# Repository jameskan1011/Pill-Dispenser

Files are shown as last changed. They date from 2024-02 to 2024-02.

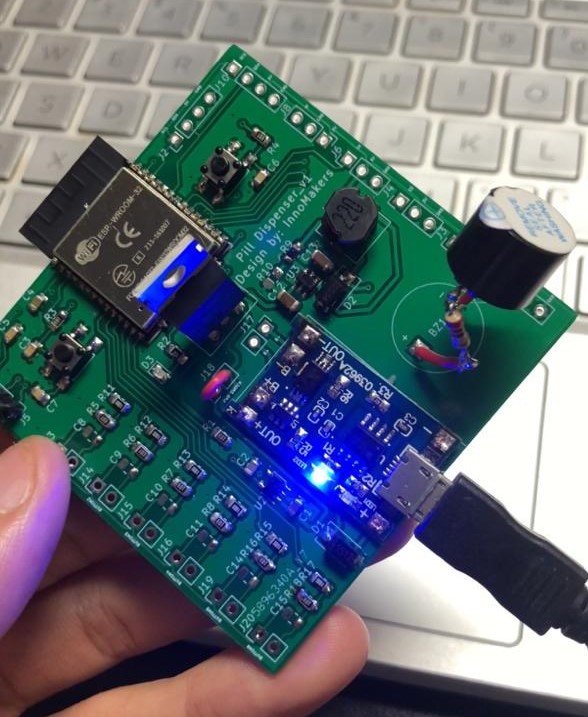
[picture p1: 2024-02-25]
Pictures/pcb.jpeg

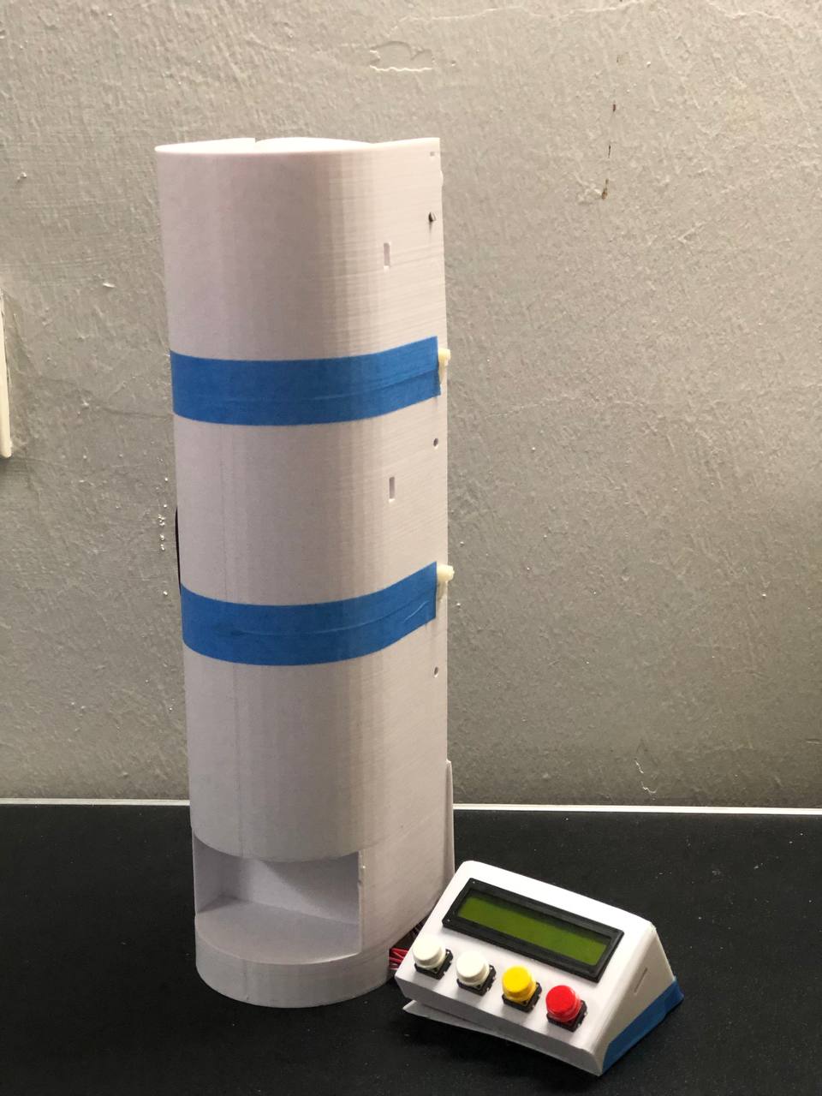
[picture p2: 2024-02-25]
Pictures/dispenser1.jpeg

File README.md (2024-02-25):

# Pill-Dispenser
Pill Dispensir with onboard settings that let you customize reminders for your meds.
<br />• Can be stack for multiple types of pill
<br />• Buzzer alert
<br />• Pill drop count
<br />• Customize time and quantities for meds.

dispenser1
pcb

https://github.com/jameskan1011/Pill-Dispenser/assets/66528008/c5491cce-084c-414e-90f5-08d18c687c19

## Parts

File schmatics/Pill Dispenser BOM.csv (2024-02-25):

Source: | C:\Users\KAN CHANG FEI\Documents\KiCad\6.0\projects\Pill Dispenser\Pill Dispenser\Pill Dispenser.kicad_sch
Date: | 4/19/2023 23:44
Tool: | Eeschema (6.0.5)
Generator: | C:\Program Files\KiCad\6.0\bin\scripting\plugins/bom_csv_grouped_by_value.py
Component Count: | 61
Collated Components:
Item | Qty | Reference(s) | Value | Unit Price | Cost | LibPart | Footprint | Datasheet
1 | 1 | BZ1 | Buzzer |  |  | Device:Buzzer | Buzzer_Beeper:Buzzer_12x9.5RM7.6 | ~
2 | 1 | C1 | 4.7uF |  |  | Device:C | Capacitor_SMD:C_0805_2012Metric | ~
3 | 2 | C2, C4 | 10uF |  |  | Device:C | Capacitor_SMD:C_0805_2012Metric | ~
4 | 10 | C3, C5, C6, C7, C8, C9, C10, C11, C14, C15 | 0.1uF |  |  | Device:C | Capacitor_SMD:C_0805_2012Metric | ~
5 | 2 | C12, C13 | 47uF |  |  | Device:C | Capacitor_SMD:C_0805_2012Metric | ~
6 | 1 | D1 | SS12 |  |  | Device:D_Schottky | Diode_SMD:D_SMA | ~
7 | 1 | D2 | SS34 |  |  | Device:D_Schottky | Diode_SMD:D_SMA | ~
8 | 1 | D3 | LED |  |  | Device:LED | LED_SMD:LED_0805_2012Metric | ~
9 | 1 | J1 | Servo1 |  |  | Connector:Conn_01x03_Male | Connector_PinHeader_2.54mm:PinHeader_1x03_P2.54mm_Vertical | ~
10 | 1 | J2 | LCD Display |  |  | Connector:Conn_01x04_Male | Connector_PinHeader_2.54mm:PinHeader_1x04_P2.54mm_Vertical | ~
11 | 1 | J3 | Servo2 |  |  | Connector:Conn_01x03_Male | Connector_PinHeader_2.54mm:PinHeader_1x03_P2.54mm_Vertical | ~
12 | 1 | J4 | Servo3 |  |  | Connector:Conn_01x03_Male | Connector_PinHeader_2.54mm:PinHeader_1x03_P2.54mm_Vertical | ~
13 | 1 | J5 | UART |  |  | Connector:Conn_01x04_Male | Connector_PinHeader_2.54mm:PinHeader_1x04_P2.54mm_Vertical | ~
14 | 1 | J6 | Servo4 |  |  | Connector:Conn_01x03_Male | Connector_PinHeader_2.54mm:PinHeader_1x03_P2.54mm_Vertical | ~
15 | 1 | J8 | IR |  |  | Connector:Conn_01x03_Male | Connector_PinHeader_2.54mm:PinHeader_1x03_P2.54mm_Vertical | ~
16 | 1 | J10 | RTC | 12.5 | 12.5 | Connector:Conn_01x04_Male | Connector_PinHeader_2.54mm:PinHeader_1x04_P2.54mm_Vertical | ~
17 | 1 | J13 | Button1 |  |  | Connector:Conn_01x02_Male | Connector_PinHeader_2.54mm:PinHeader_1x02_P2.54mm_Vertical | ~
18 | 1 | J14 | Button2 |  |  | Connector:Conn_01x02_Male | Connector_PinHeader_2.54mm:PinHeader_1x02_P2.54mm_Vertical | ~
19 | 1 | J15 | Button3 |  |  | Connector:Conn_01x02_Male | Connector_PinHeader_2.54mm:PinHeader_1x02_P2.54mm_Vertical | ~
20 | 1 | J16 | Button4 |  |  | Connector:Conn_01x02_Male | Connector_PinHeader_2.54mm:PinHeader_1x02_P2.54mm_Vertical | ~
21 | 1 | J17 | BAttery |  |  | Connector:Conn_01x02_Male | Connector_PinHeader_2.54mm:PinHeader_1x02_P2.54mm_Vertical | ~
22 | 1 | J18 | Power Switch |  |  | Connector:Conn_01x02_Male | Connector_PinHeader_2.54mm:PinHeader_1x02_P2.54mm_Vertical | ~
23 | 1 | J19 | Button5 |  |  | Connector:Conn_01x02_Male | Connector_PinHeader_2.54mm:PinHeader_1x02_P2.54mm_Vertical | ~
24 | 1 | J20 | Button6 |  |  | Connector:Conn_01x02_Male | Connector_PinHeader_2.54mm:PinHeader_1x02_P2.54mm_Vertical | ~
25 | 1 | L1 | 22uH |  |  | pspice:INDUCTOR | Inductor_SMD:L_7.3x7.3_H4.5 | ~
26 | 1 | Q1 | IRF4905 |  |  | Transistor_FET:IRF9540N | Package_TO_SOT_THT:TO-220-3_Vertical | http://www.irf.com/product-info/datasheets/data/irf9540n.pdf
27 | 9 | R1, R3, R4, R5, R6, R7, R8, R16, R18 | 10K |  |  | Device:R | Resistor_SMD:R_0805_2012Metric_Pad1.20x1.40mm_HandSolder | ~
28 | 1 | R2 | 1K |  |  | Device:R | Resistor_SMD:R_0805_2012Metric_Pad1.20x1.40mm_HandSolder | ~
29 | 1 | R9 | 14.7K |  |  | Device:R | Resistor_SMD:R_0805_2012Metric_Pad1.20x1.40mm_HandSolder | ~
30 | 1 | R10 | 2K |  |  | Device:R | Resistor_SMD:R_0805_2012Metric_Pad1.20x1.40mm_HandSolder | ~
31 | 6 | R11, R12, R13, R14, R15, R17 | 100 |  |  | Device:R | Resistor_SMD:R_0805_2012Metric_Pad1.20x1.40mm_HandSolder | ~
32 | 2 | SW1, SW2 | SW_SPST |  |  | Switch:SW_SPST | Button_Switch_SMD:SW_SPST_TL3305A | ~
33 | 1 | U1 | TP4056_Module |  |  | My_Design:TP4056_Module | My_Design:TP4056_Module
34 | 1 | U2 | AP7366-33W5-7 |  |  | Regulator_Linear:MIC5504-3.3YM5 | Package_TO_SOT_SMD:SOT-23-5_HandSoldering | http://ww1.microchip.com/downloads/en/DeviceDoc/MIC550X.pdf
35 | 1 | U3 | MT3608 |  |  | Regulator_Switching:MT3608 | Package_TO_SOT_SMD:SOT-23-6 | https://www.olimex.com/Products/Breadboarding/BB-PWR-3608/resources/MT3608.pdf
36 | 1 | U4 | ESP32-WROOM-32 | 10 | 10 | RF_Module:ESP32-WROOM-32 | RF_Module:ESP32-WROOM-32 | https://www.espressif.com/sites/default/files/documentation/esp32-wroom-32_datasheet_en.pdf

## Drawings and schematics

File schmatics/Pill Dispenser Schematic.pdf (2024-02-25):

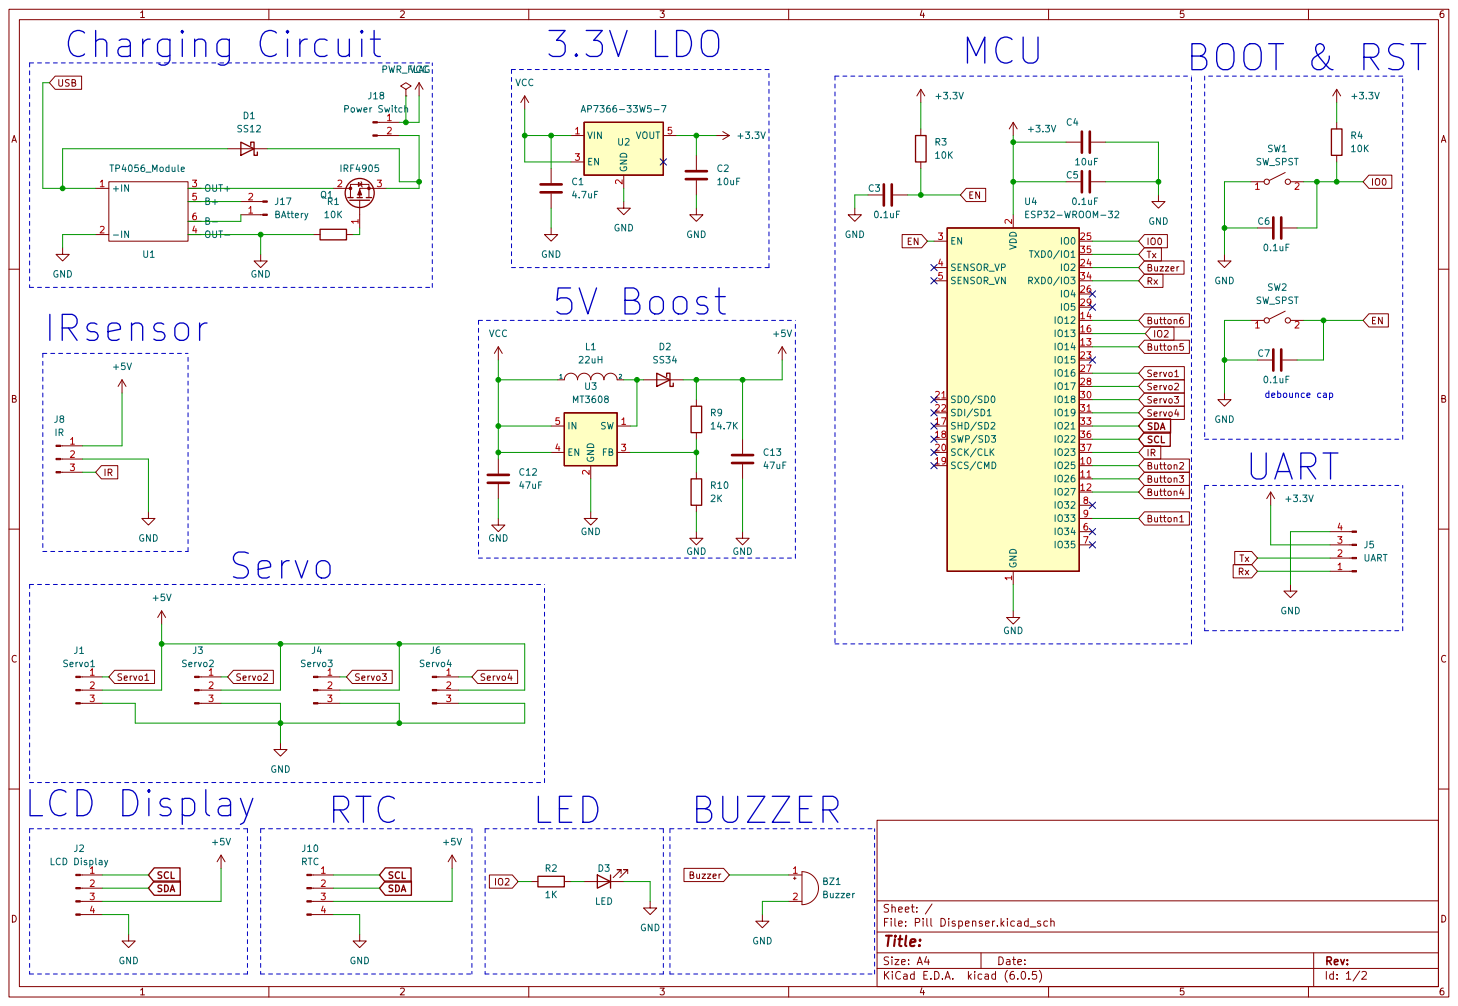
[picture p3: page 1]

2 EN 3 VOUT 5 U2 AP7366-33W5-7 D2 SS34 GND GNDGND

2 SCK/CLK 20 SDO/SD0 21 SDI/SD1 22

File: Pill Dispenser.kicad_sch Sheet: / Untitled Sheet File: untitled.kicad_sch

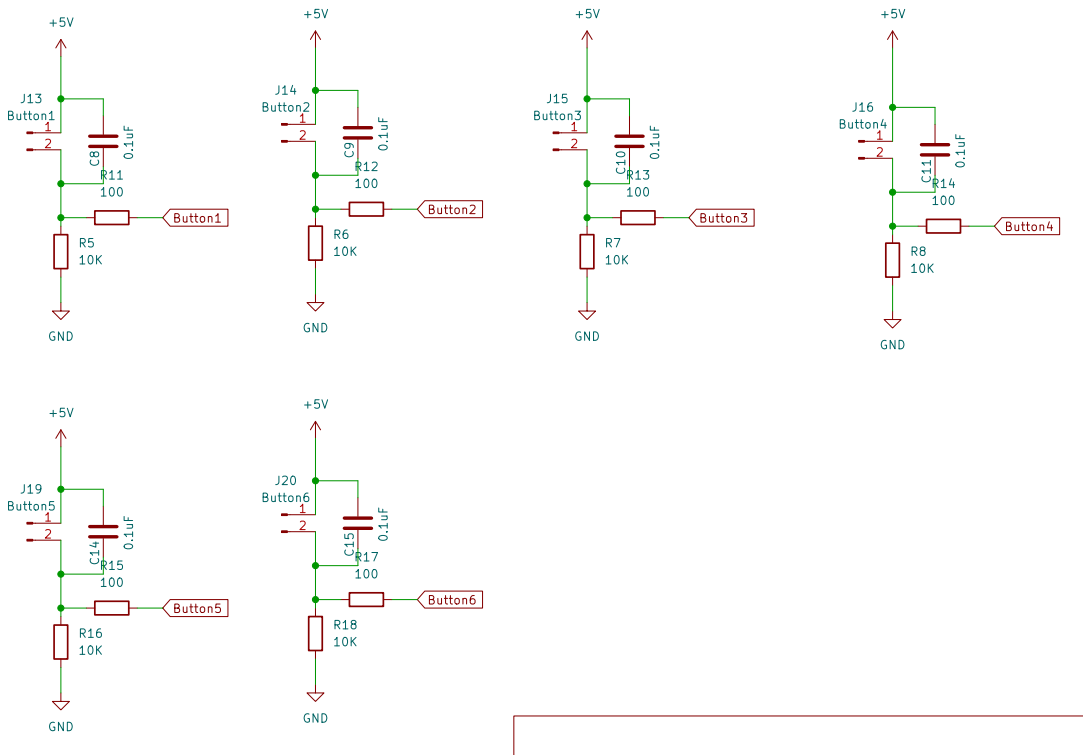
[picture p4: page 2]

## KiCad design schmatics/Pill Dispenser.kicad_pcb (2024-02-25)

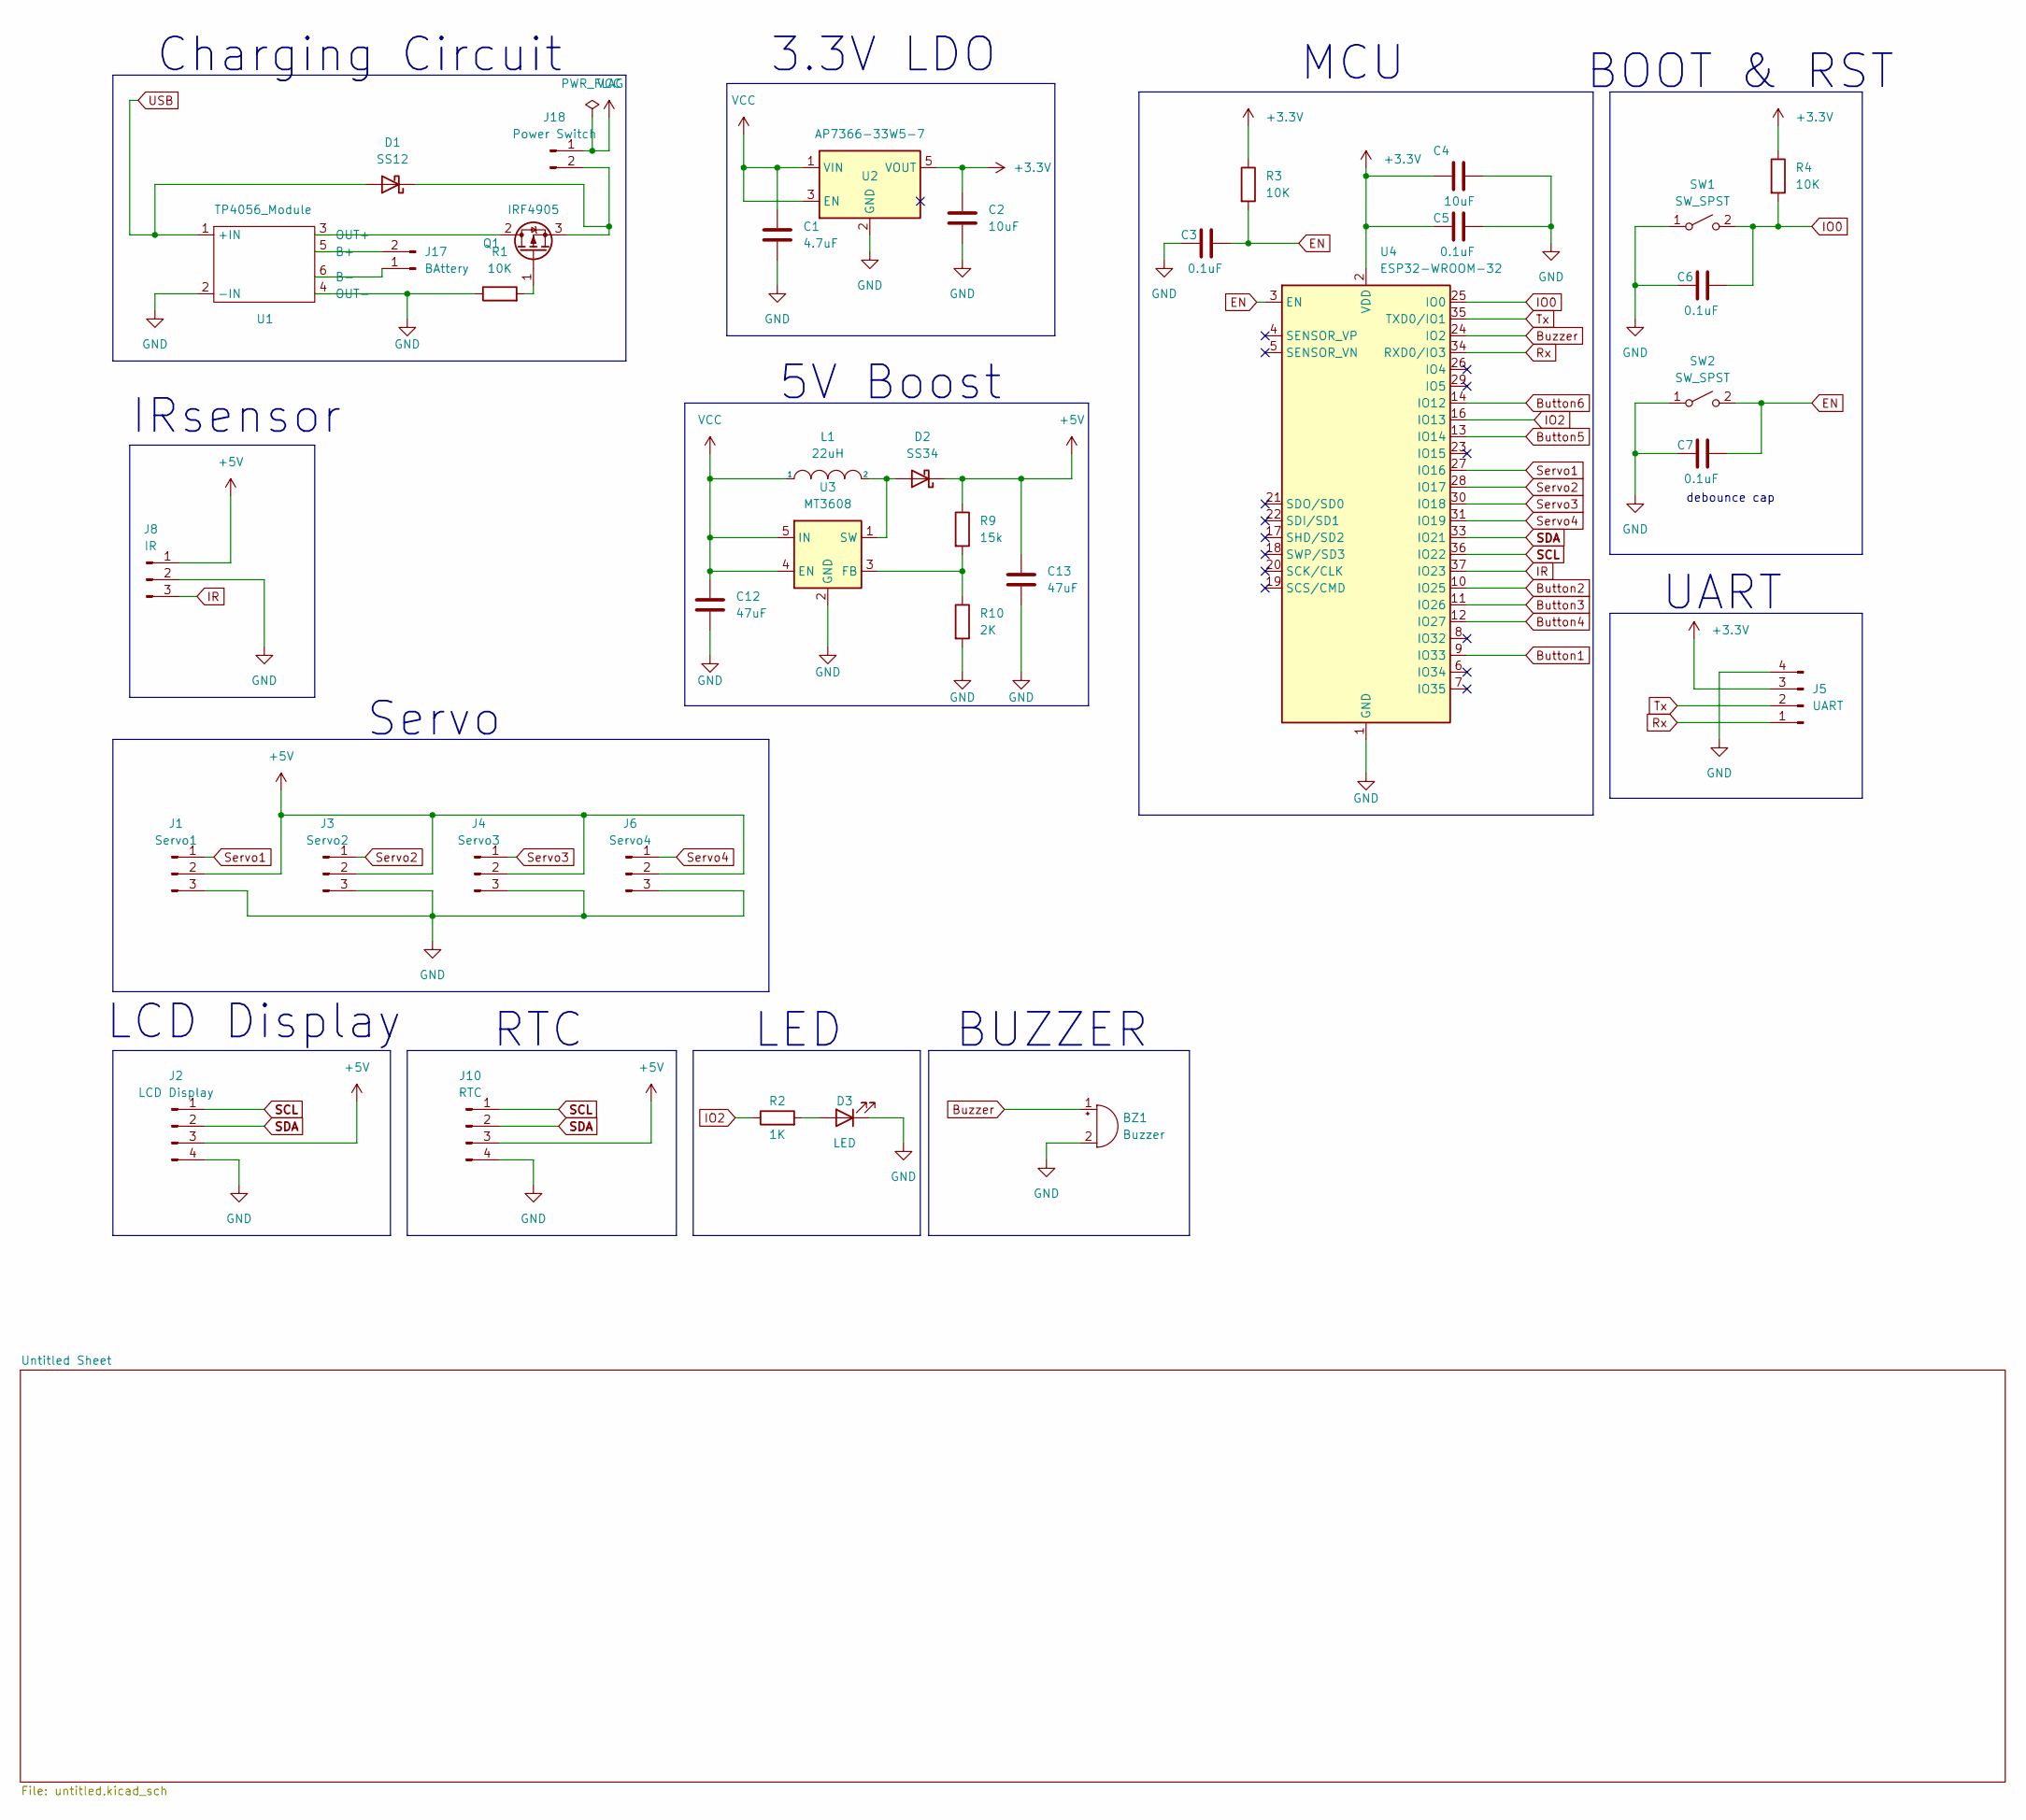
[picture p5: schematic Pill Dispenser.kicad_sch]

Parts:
BZ1: Buzzer; Buzzer_12x9.5RM7.6
C1: 4.7uF; C_0805_2012Metric
C2, C4: 10uF; C_0805_2012Metric
C3, C5, C6, C7: 0.1uF; C_0805_2012Metric
C12, C13: 47uF; C_0805_2012Metric
D1: SS12; D_SMA
D2: SS34; D_SMA
D3: LED; LED_0805_2012Metric
J1: Servo1; PinHeader_1x03_P2.54mm_Vertical
J2: LCD Display; PinHeader_1x04_P2.54mm_Vertical
J3: Servo2; PinHeader_1x03_P2.54mm_Vertical
J4: Servo3; PinHeader_1x03_P2.54mm_Vertical
J5: UART; PinHeader_1x04_P2.54mm_Vertical
J6: Servo4; PinHeader_1x03_P2.54mm_Vertical
J8: IR; PinHeader_1x03_P2.54mm_Vertical
J10: RTC; PinHeader_1x04_P2.54mm_Vertical
J17: BAttery; PinHeader_1x02_P2.54mm_Vertical
J18: Power Switch; PinHeader_1x02_P2.54mm_Vertical
L1: 22uH; L_7.3x7.3_H4.5
Q1: IRF4905; TO-220-3_Vertical
R1, R3, R4: 10K; R_0805_2012Metric_Pad1.20x1.40mm_HandSolder
R2: 1K; R_0805_2012Metric_Pad1.20x1.40mm_HandSolder
R9: 15k; R_0805_2012Metric_Pad1.20x1.40mm_HandSolder
R10: 2K; R_0805_2012Metric_Pad1.20x1.40mm_HandSolder
SW1, SW2: SW_SPST; SW_SPST_TL3305A
U1: TP4056_Module
U2: AP7366-33W5-7; SOT-23-5_HandSoldering
U3: MT3608; SOT-23-6
U4: ESP32-WROOM-32

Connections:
+3V3: C2.1, C4.1, C5.1, J5.3, R3.1, R4.1, U2.5 (VOUT), U4.2 (VDD)
+5V: C13.1, D2.1 (K), J1.2, J2.3, J3.2, J4.2, J6.2, J8.1, J10.3, R9.1; also elsewhere on the board
Button1: U4.9 (IO33); also elsewhere on the board
Button2: U4.10 (IO25); also elsewhere on the board
Button3: U4.11 (IO26); also elsewhere on the board
Button4: U4.12 (IO27); also elsewhere on the board
Button5: U4.13 (IO14); also elsewhere on the board
Button6: U4.14 (IO12); also elsewhere on the board
Buzzer: BZ1.1 (-), U4.24 (IO2)
EN: C3.2, C7.2, R3.2, SW2.2 (B), U4.3 (EN)
GND: BZ1.2 (+), C1.2, C2.2, C3.1, C4.2, C5.2, C6.1, C7.1, C12.2, C13.2, D3.1 (K), J1.3, J2.4, J3.3, J4.3, J5.4, J6.3, J8.2, J10.4, R1.1, R10.2, SW1.1 (A), SW2.1 (A), U1.2 (-IN), U1.4 (OUT-), U2.2 (GND), U3.2 (GND), U4.1 (GND), U4.15 (GND), U4.38 (GND), U4.39 (GND); also elsewhere on the board
IO0: C6.2, R4.2, SW1.2 (B), U4.25 (IO0)
IO2: R2.1, U4.16 (IO13)
IR: J8.3, U4.37 (IO23)
unnamed: D1.1 (K), J18.2, Q1.3 (S)
unnamed: D2.2 (A), L1.2, U3.1 (SW)
unnamed: D3.2 (A), R2.2
unnamed: J17.1, U1.6 (B-)
unnamed: J17.2, U1.5 (B+)
unnamed: Q1.1 (G), R1.2
unnamed: Q1.2 (D), U1.3 (OUT+)
unnamed: R9.2, R10.1, U3.3 (FB)
Rx: J5.1, U4.34 (RXD0/IO3)
SCL: J2.1, J10.1, U4.36 (IO22)
SDA: J2.2, J10.2, U4.33 (IO21)
Servo1: J1.1, U4.27 (IO16)
Servo2: J3.1, U4.28 (IO17)
Servo3: J4.1, U4.30 (IO18)
Servo4: J6.1, U4.31 (IO19)
Tx: J5.2, U4.35 (TXD0/IO1)
USB: D1.2 (A), U1.1 (+IN)
VCC: C1.1, C12.1, J18.1, L1.1, U2.1 (VIN), U2.3 (EN), U3.4 (EN), U3.5 (IN)

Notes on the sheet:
Charging Circuit
Servo
MCU
BOOT & RST
3.3V LDO
LCD Display
5V Boost
BUZZER
debounce cap
LED
UART
RTC
IRsensor

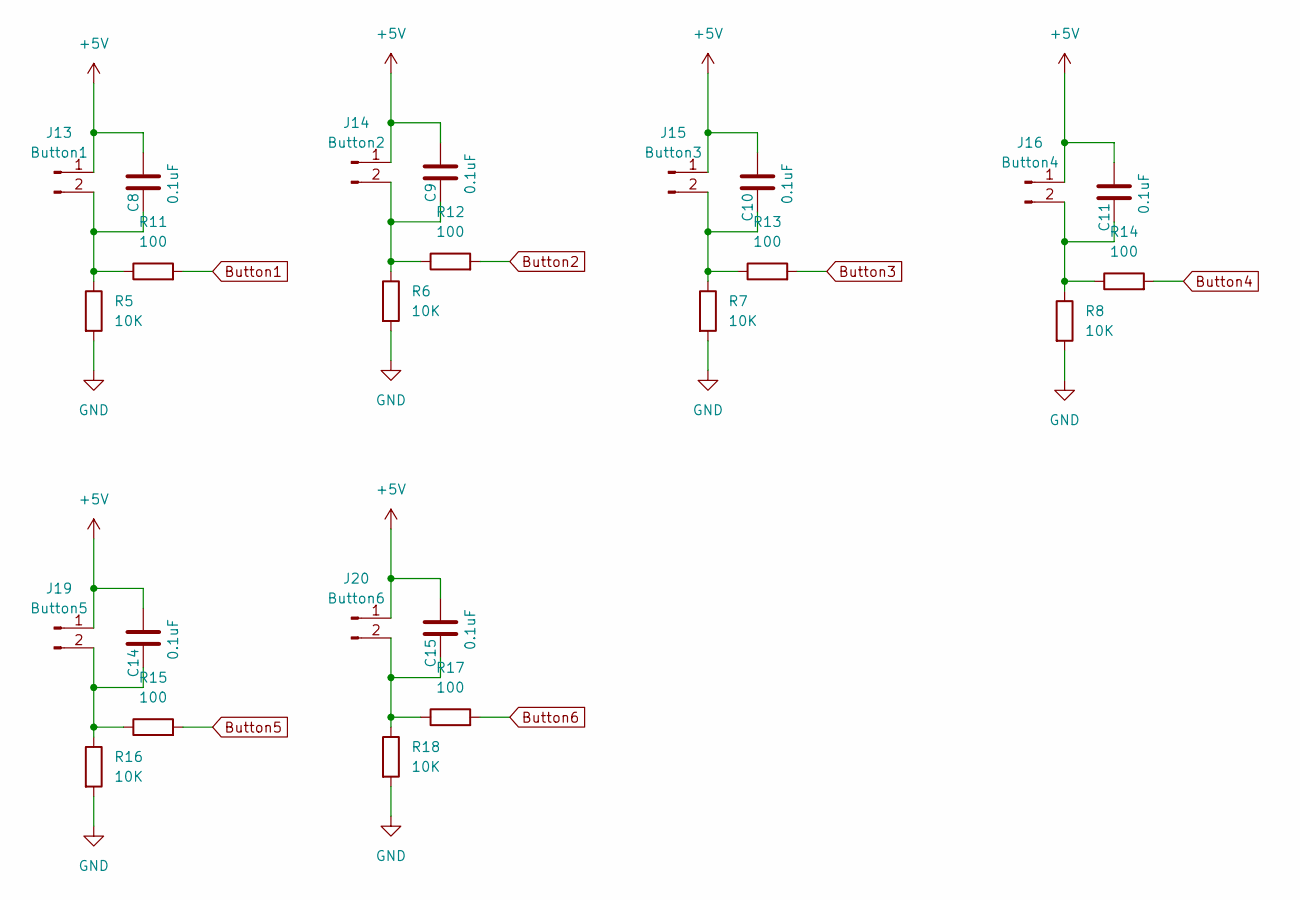
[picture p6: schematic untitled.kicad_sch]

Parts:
C8, C9, C10, C11, C14, C15: 0.1uF; C_0805_2012Metric
J13: Button1; PinHeader_1x02_P2.54mm_Vertical
J14: Button2; PinHeader_1x02_P2.54mm_Vertical
J15: Button3; PinHeader_1x02_P2.54mm_Vertical
J16: Button4; PinHeader_1x02_P2.54mm_Vertical
J19: Button5; PinHeader_1x02_P2.54mm_Vertical
J20: Button6; PinHeader_1x02_P2.54mm_Vertical
R5, R6, R7, R8, R16, R18: 10K; R_0805_2012Metric_Pad1.20x1.40mm_HandSolder
R11, R12, R13, R14, R15, R17: 100; R_0805_2012Metric_Pad1.20x1.40mm_HandSolder

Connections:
+5V: C8.2, C9.2, C10.2, C11.2, C14.2, C15.2, J13.1, J14.1, J15.1, J16.1, J19.1, J20.1; also elsewhere on the board
Button1: R11.2; also elsewhere on the board
Button2: R12.2; also elsewhere on the board
Button3: R13.2; also elsewhere on the board
Button4: R14.2; also elsewhere on the board
Button5: R15.2; also elsewhere on the board
Button6: R17.2; also elsewhere on the board
GND: R5.2, R6.2, R7.2, R8.2, R16.2, R18.2; also elsewhere on the board
unnamed: C8.1, J13.2, R5.1, R11.1
unnamed: C9.1, J14.2, R6.1, R12.1
unnamed: C10.1, J15.2, R7.1, R13.1
unnamed: C11.1, J16.2, R8.1, R14.1
unnamed: C14.1, J19.2, R15.1, R16.1
unnamed: C15.1, J20.2, R17.1, R18.1

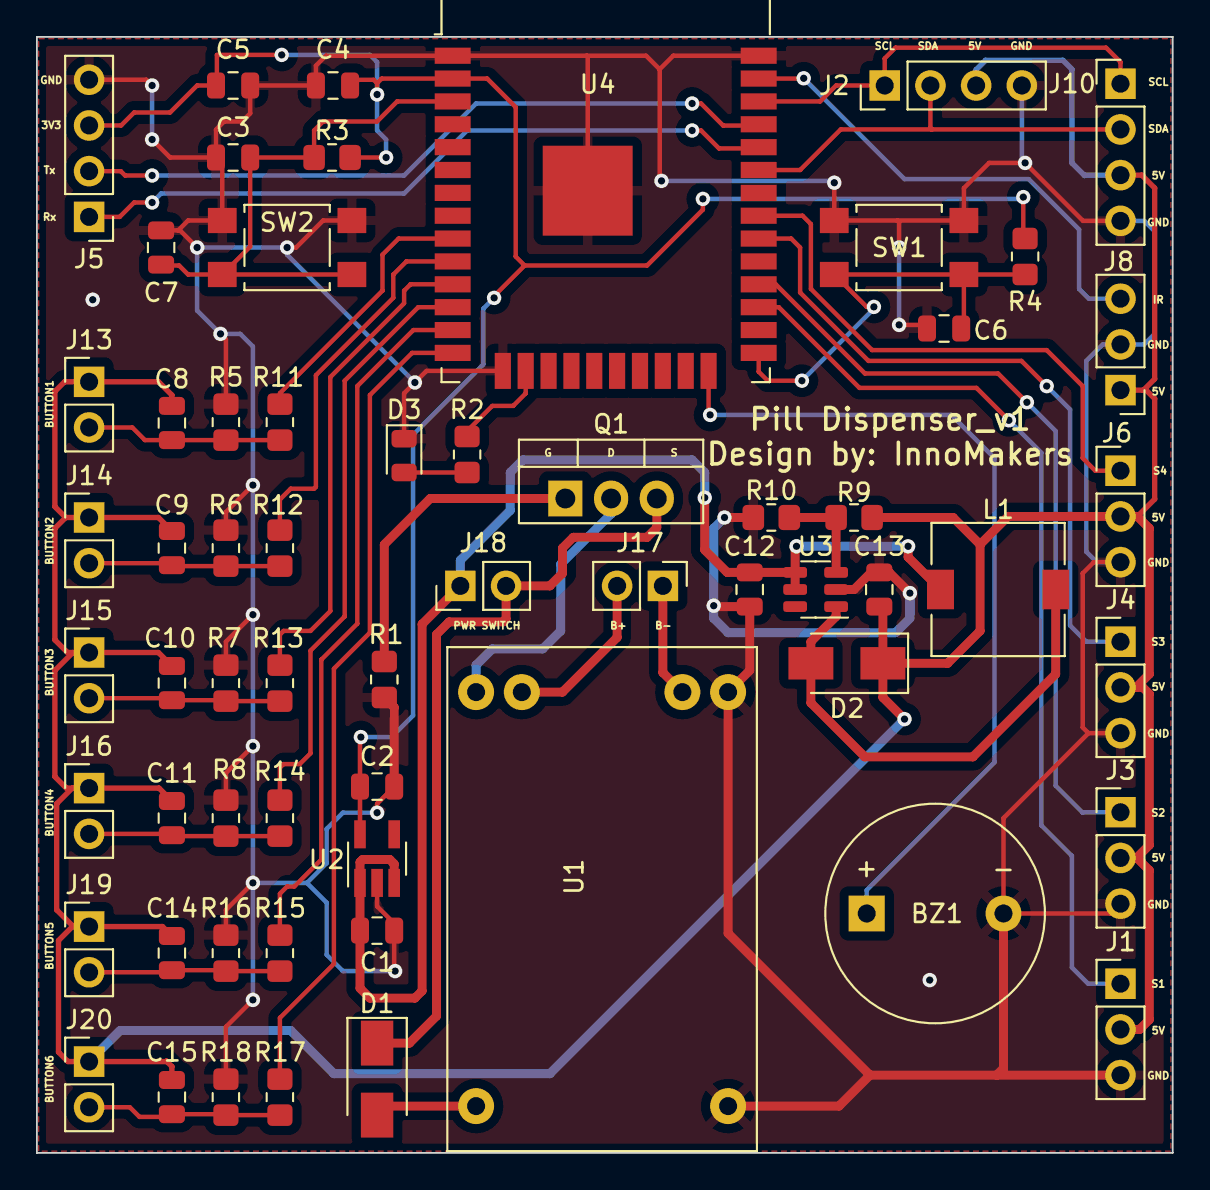
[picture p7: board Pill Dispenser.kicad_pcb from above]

Board: 2 copper layers, 63.1 x 62.0 mm, 61 parts (0 on the bottom side), 38 nets.

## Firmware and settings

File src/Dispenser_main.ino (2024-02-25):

#include "RTC.h"
#include "LCD_Display.h"
#include "Button.h"
#include "Buzzer.h"
#include "ServoMotor.h"
#include "IR_Counter.h"
//#include "Firebase_data.h"
#define ONBOARD_LED  2


void setup() {
  // put your setup code here, to run once:
  Serial.begin(115200);
  InitButton();
  setupRTC();
  setupBuzzer();
  setupServo();
  InitLCD();
  //setupFirebase();
  // pinMode(ONBOARD_LED, OUTPUT);

}

void loop() {
  DateTime now = getTimeRTC();
  ReadButton();
  DisplayMenu();
  checkMedicationTime(now);
   //sendDataToFirebase("Pill1/number", 2);

  //Serial.println(now.hour());
  // put your main code here, to run repeatedly:

}

void checkMedicationTime(DateTime now){
  
  //DateTime now = getTimeRTC();
  if (now.hour() == startTimeToTake1) {
      Serial.println("pills A");

      sensorDetectionCount = 0;

      for(int i =0; i < pillsToTake1;){
      if (sensorDetectionCount == i) 
       {
      Serial.print("Dispense Pill: ");
      Serial.println(i);
      dispensePill(1);
      i++;
       }
       else {
          dispensePill(1);
        }
       count();
    }
      // Update the next medication time for A
      startTimeToTake1 = startTimeToTake1 + intervalToTake1;
    }

  else if (now.hour() == startTimeToTake2) {
    Serial.println("pills B");

     sensorDetectionCount = 0;

    
    // Dispense pills for medication type 2
   for(int i =0; i < pillsToTake2;){
      if (sensorDetectionCount == i) 
       {
      Serial.print("Dispense Pill: ");
      Serial.println(i);
      dispensePill(2);
      i++;
       }
       else {
          dispensePill(2);
        }
       count();
    }
    // Update the next medication time for B
    startTimeToTake2 = startTimeToTake2 + intervalToTake2;
  }

  else if (now.hour() == startTimeToTake3) {
    Serial.println("pills C");

     sensorDetectionCount = 0;
    
    for(int i =0; i < pillsToTake3;){
      if (sensorDetectionCount == i) 
       {
      Serial.print("Dispense Pill: ");
      Serial.println(i);
      dispensePill(3);
      i++;
       }
       else {
          dispensePill(3);
        }
       count();
    }
    
    startTimeToTake3 = startTimeToTake3 + intervalToTake3;
  }

  else if (now.hour() == startTimeToTake4) {
    Serial.println("pills D");

     sensorDetectionCount = 0;
    
    for(int i =0; i < pillsToTake4;){
      if (sensorDetectionCount == i) 
       {
      Serial.print("Dispense Pill: ");
      Serial.println(i);
      dispensePill(4);
      i++;
       }
       else {
          dispensePill(4);
        }
       count();
    }
    
    startTimeToTake4 = startTimeToTake4 + intervalToTake4;
  }
  else 
  offBuzzer();
}

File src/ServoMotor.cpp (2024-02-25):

#include "ServoMotor.h"
#include <Arduino.h>
#include "IR_Counter.h"

Servo servo1; 
Servo servo2; 
Servo servo3; 
Servo servo4; 

// int pos1 = 0;
// int pos2 = 0;
// int pos3 = 0;
// int pos4 = 0;

void setupServo() {
  servo1.attach(16);
  servo1.write(0);
  servo2.attach(17);
  servo2.write(0);
  servo3.attach(18);
  servo3.write(0);
  servo4.attach(19);
  servo4.write(0);
}

void dispensePill(int pillType) {
  switch(pillType) {
      case 1:
        for (int pos1 = 0; pos1 <= 180; pos1 += 10) { // goes from 0 degrees to 180 degrees
		// in steps of 1 degree
	      servo1.write(pos1);    // tell servo to go to position in variable 'pos'
	      delay(100);             // waits 15ms for the servo to reach the position
        count();
	}
	      for (int pos1 = 180; pos1 >= 0; pos1 -= 10) { // goes from 180 degrees to 0 degrees
		    servo1.write(pos1);    // tell servo to go to position in variable 'pos'
		    delay(100);             // waits 15ms for the servo to reach the position
        count();
	}
        
        break;
      case 2:
        for (int pos2 = 0; pos2 <= 180; pos2 += 10) { // goes from 0 degrees to 180 degrees
		// in steps of 1 degree
	      servo2.write(pos2);    // tell servo to go to position in variable 'pos'
	      delay(100);             // waits 15ms for the servo to reach the position
        count();
	}
	      for (int pos2 = 180; pos2 >= 0; pos2 -= 10) { // goes from 180 degrees to 0 degrees
		    servo2.write(pos2);    // tell servo to go to position in variable 'pos'
		    delay(100);             // waits 15ms for the servo to reach the position
        count();
	}
        break;
      case 3:
        for (int pos3 = 0; pos3 <= 180; pos3 += 10) { // goes from 0 degrees to 180 degrees
		// in steps of 1 degree
	      servo3.write(pos3);    // tell servo to go to position in variable 'pos'
	      delay(100);             // waits 15ms for the servo to reach the position
        count();
	}
	      for (int pos3 = 180; pos3 >= 0; pos3 -= 10) { // goes from 180 degrees to 0 degrees
		    servo3.write(pos3);    // tell servo to go to position in variable 'pos'
		    delay(100);             // waits 15ms for the servo to reach the position
        count();
	}
        break;
      case 4:
        for (int pos4 = 0; pos4 <= 180; pos4 += 10) { // goes from 0 degrees to 180 degrees
		// in steps of 1 degree
	      servo4.write(pos4);    // tell servo to go to position in variable 'pos'
	      delay(100);             // waits 15ms for the servo to reach the position
        count();
	}
	      for (int pos4 = 180; pos4 >= 0; pos4 -= 10) { // goes from 180 degrees to 0 degrees
		    servo4.write(pos4);    // tell servo to go to position in variable 'pos'
		    delay(100);             // waits 15ms for the servo to reach the position
        count();
	}
        break;
      default:
        // handle invalid pill type
        Serial.println("Invalid pill type!");
}
}
